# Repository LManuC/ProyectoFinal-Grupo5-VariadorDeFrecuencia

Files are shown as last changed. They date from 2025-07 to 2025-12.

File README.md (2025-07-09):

# ProyectoFinal-Grupo5-VariadorDeFrecuencia
El presente proyecto propone el desarrollo de un dispositivo electrónico capaz de alimentar un motor trifásico de hasta 1/3 HP, utilizando como fuente una tensión continua de 12V. Este conversor funciona como un variador de frecuencia, generando una salida trifásica con tensión eficaz entre fases de hasta 220 Vrms y frecuencia de salida variable entre 1 Hz y 150 Hz.
Para lograr el control del motor, se utiliza una técnica de modulación espacial (Space Vector Modulation), sin sensores montados en el eje del motor, lo que permite una instalación más sencilla, sin necesidad de encoder. El sistema está comandado por un controlador que gestiona tanto el disparo de los transistores como la interfaz de usuario y las protecciones internas.
El sistema estará contenido en una carcasa plástica especialmente diseñada para garantizar seguridad eléctrica durante la manipulación, proteger los componentes internos y permitir un montaje simple y robusto en el entorno de uso.

# Motivación
En un país como la Argentina, con grandes extensiones de tierras sin suministro eléctrico, la explotación de la energía renovable ha dado lugar a la utilización de grandes máquinas y herramientas eléctricas que tiempo atrás no hubiese sido posible. Si bien es cierto que los generadores eléctricos han dado espacio a estas instalaciones, requerían de mantenimiento periódico para que estuviesen operativas en el momento que se necesitaban, además de necesitar un material combustible que les permitiera funcionar y, en ocasiones podría generar un problema el ruido de los motores.

# Concepto del negocio
El dispositivo diseñado permitirá la conversión, acondicionamiento y regulación de la energía eléctrica para el accionamiento de un motor trifásico de baja potencia (1/3 HP) con velocidad variable generada a partir del motor de combustión interna y el alternador de equipos agrícolas o sistemas de energía solar, eólica con su correspondiente back up de energía eléctrica, posibilitando la operación de motores trifásicos destinados a tareas como sistemas de riego, transporte de materiales mediante cintas motorizadas o procesos de molienda integrados a bordo que puedan emplearse unificando todos los dispositivos que son empleados en instalaciones de energía renovable: Elevadores de tensión, inversores y variadores de frecuencia. La propuesta se enmarca en la necesidad de implementar soluciones energéticas autónomas y portátiles en entornos rurales, donde las condiciones de acceso a la red eléctrica convencional pueden ser limitadas o inexistentes.

## FODA

### Fortalezas
* La alimentación de baja tensión, nos permite meternos en un nuevo nicho. Permite trabajar con sistemas solares reducidos o baterías.
* Producto robusto y económico.
* Mantenimiento preventivo y reparación: Al conocer el diseño del equipo se puede hacer mantenimiento a los equipos y también otorgar una garantía con un taller de revisión y reparación en caso de falla.
* Productor local: Es una característica muy importante ya que el cliente tiene mayor confianza y los plazos de entrega son muchos más rápidos y económicos.
### Oportunidades
* Dada la practicidad puede ocasionar una gran demanda en zonas aisladas, remotas o rurales que se encuentren offgrid.
* Dado que es un único producto de su clase podría aparecer un nuevo rubro o sector diferente en donde encuentre utilidad. 
* El desarrollo nacional nos puede dar ventajas en licitaciones públicas o incentivos tecnológicos del gobierno.
### Debilidades
* Falta de experiencia y desconocimiento del producto puede desalentar o generar desconfianza en el producto.
* La robustez es muy importante en un controlador de un motor, se necesitan años de estudio riguroso del comportamiento y testeo del equipo para asegurar un funcionamiento ejemplar.
* La certificación eléctrica es un aspecto crucial en un equipo de esta clase y estas son muy costosas.
### Amenazas
* Posibilidad de la aparición de competencia con mejores precios y más funcionalidades.
* La escalabilidad no siempre es tan lineal, si aumenta mucho el mercado puede ocurrir que la inversión sea grande.
* El soporte post venta debe funcionar bien ya que en caso de una respuesta lenta al cliente podría perjudicar a la reputación de la marca.

# Alcance
El alcance del proyecto quedará definido en lograr, a partir de una fuente de de 12V de corriente contínua, el accionamiento de un motor trifásico de ⅓ de HP, variar su velocidad de giro, programar sesiones de trabajo diario, informar por señales típicas de 0-10V la velocidad de operación del motor, parada de emergencia, configuración de velocidades a través de un selector.

## Características eléctricas del dispositivo
Vin: 12VDC
Vout: 3 x 220VAC
fout: 0Hz - 150Hz
Pmax: 375W / 1/2HP

# Riesgos
1.  Fallas en la elección de la topología:
    -  Priorización del diseño frente a otras tareas;
    -  Ensayos varios sobre circuitos físicos;
2.  Rendimiento simulado insuficiente
    -  Priorización del diseño frente a otras tareas;
    -  Ensayos varios sobre circuitos físicos;
    -  Pruebas sobre motores utilizando variadores de frecuencia comerciales con entrada de contínua;
3.  No se consiguen los materiales en el mercado local
    -  Diseño temprano de PCB
    -  Compra en exceso de dispositivos críticos
4.  El transformador está mal construído y no entrega la potencia necesaria
    -  Fabricación de transformador con un proveedor especializado
5.  Al PCB le faltaron rutear una o más pistas
    -  Validaciones cruzadas de footprints
    -  Validaciones cruzadas de esquemáticos
    -  Validaciones cruzadas de PCB
6.  Pérdida de componentes
    -  Compra en exceso de dispositivos críticos
    -  Compra en exceso de dispositivos pequeños
    -  Compra en exceso de dispositivos sin marking
7.  Error en el diseño del footprint
    -  Validaciones cruzadas de footprints
    -  Checkbox en componentes para registrar validación
    -  Agregado de hoja de datos al esquemático
    -  Agregado de nombre del componente según el fabricante
8.  Errores de diseño hacen que la tensión no sea lo suficientemente alta
    -  Diseño autodefensivo con tensiones sobredimensionadas
    -  Cálculo de convertido con duty de respaldo
9. Rotura del banco de pruebas
    -  Fabricación de partes críticas de repuesto
    -  Colaboración externa especializada
10. Dificultades para simular el desfasaje
    -  Sobreestimación de los tiempos de trabajo
11. Error en el cálculo de la corriente máxima de algún componente y la corriente quedó sobredimensionada
    -  Justificación y documentación de los componentes elegidos
    -  Compra en exceso de dispositivos críticos
12. Falla el circuito y se quema una de las placas de potencia
    -  Fabricación de placa extra
    -  Compra en exceso de dispositivos críticos
    -  Circuitería de protección ruteada sin montar
13. El transformador está mal calculado y no entrega la potencia necesaria
    -  Ensayos exhaustivos durante el diseño
14. Ruido eléctrico interfiere en el display
    -  Fabricación de pantalla metálica para separar circuitos ruidosos
15. El motor no arranca por falta de potencia en la entrada
    -  Pruebas con batería de auto de respaldo

# Calidad

|Funcionalidad |  Importancia  |
|---|---|
|Tensión de salida |  16,3% |
|Tensión entrada |  20,7% |
|Frecuencia de salida | 7,1% |
|Protecciones contra sobrecorriente| 6,9% |
|Aislamiento entrada salida |  12,1% |
|Algoritmo modulación | 9,6% |
|Display con menú |  10,6% |
|GPIOs | 7,7% |
|Access point | 9,0% |

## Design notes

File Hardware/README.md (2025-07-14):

# Comunicación entre microcontraldores

## 1. UART (Universal Asynchronous Receiver/Transmitter)
_Tipo:_ Asíncrona

_Velocidad típica:_ Hasta 1 Mbps (aunque la mayoría trabaja entre 9600 y 115200 bps)

_Ventajas:_
* Muy simple de implementar (incluso por software si no hay hardware UART)
* No necesita reloj compartido

_Desventajas:_
* Sin verificación de integridad robusta
* Solo útil para distancias cortas

_Ideal para:_ Comunicación punto a punto a distancias cortas y baja/moderada velocidad

## 2. SPI (Serial Peripheral Interface)
_Tipo:_ Síncrona (requiere línea de reloj)

_Velocidad típica:_ De 1 a 20 Mbps (puede llegar a más dependiendo del microcontrolador)

_Ventajas:_
* Muy rápida
* Full duplex
* Buena para cortas distancias dentro de un mismo PCB

_Desventajas:_
* Requiere más pines (MOSI, MISO, SCLK y a veces CS)
* No hay detección de errores integrada

_Ideal para:_ Comunicación rápida entre micros en un mismo sistema o módulo

## Conclusión

Elegimos SPI por subre UART para poder aprovechar más la velocidad del bus. Creemos que la implemetación en software no debería cambiar entre una u otra, por lo que no habría una ventaja o desventaja de una sobre la otra.

Debemos tener el cuidado suficiente de la con la señal ya que, pese a ser un único producto y un ansamblado fijo, la comunicación se dará entre dos PCBs diferentes a través de un header.

# Pulsadores

Para el traclado matricial utilizaremos los pulsadores con vástago sobresaliente para poder enganchar con la tecla impresa.

# Teclado

Utilizar por lo menos 8 teclas, pero no más (o no mucho más de 10).

El Start y stop cuentan dentro de este teclaod matricial pero el botón golpe de puño para parada de emergencia iría aparte.

Usaríamos un relay para cortar en bus de contínua, comandado por la parada de emergencia y el STM32.

# Dimensiones

El gabinete va a tener un tamaño de 130mm x 325mm (Sujeto a modificaciones) para respetar una relación de aspecto de 2.5.

La idea sería incluir en la parte superior un cooler de 120mm de lado.

# Señales a medir por el ESP

* Nivel de tensión del bus de contínua
* Corriente del bus de contínua

# Conectores

## Señales para el ADC
1. 5V
2. GND
3. Corriente
4. Tensión
5. GND

## Comunicaciones
1. GND
2. NSS
3. SCK
4. MISO
5. MOSI

## Señales de una placa a la otra

1. 0-10V
2. Selección de velocidades
3. Start
4. Stop

## Botones de start y stop

Borneras externas para conectar pulsadores externos en caso de montar el gabinete del producto dentro de otro gabinete.

# Alimentación

1. +12V
2. GND

1. +5V
2. GND

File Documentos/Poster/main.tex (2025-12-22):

\def\footer#1{\def\insertfooter{#1}}
\documentclass[final]{beamer}

\usepackage[scale=1.150]{beamerposter}
\usetheme{MUWposter}

%Logo/Banner de la Empresa/Proyecto
\logo{
\pgfputat{
\pgfxy(-10,108)}{
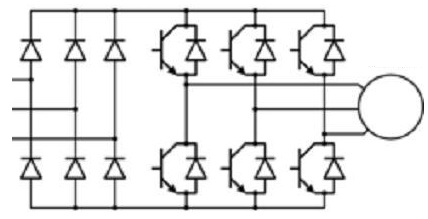
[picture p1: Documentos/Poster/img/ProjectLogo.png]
\pgfbox[center,base]{}
}
}  

\usepackage{multicol}
\usepackage{array}
\newcolumntype{L}{>{\arraybackslash}m{22cm}}
\newcolumntype{S}{>{\arraybackslash}m{5cm}}
\usepackage{pgf}  
\usepackage{mathtools}
\usepackage{amsmath, amsthm, amssymb, amsfonts}
\usepackage{exscale}
\usepackage{xcolor}
\usepackage{ushort}
\usepackage{setspace}
\usepackage[square,numbers]{natbib}
\usepackage{url}
\bibliographystyle{abbrvnat}
\renewcommand{\vec}[1]{\ushort{#1}}
\renewcommand{\vec}[1]{\mathbf{#1}}
\definecolor{greenMUW}{RGB}{60,191,174}
\definecolor{blueMUW}{RGB}{17,29,79}
\definecolor{skinMUW}{RGB}{254,228,217}
\definecolor{hellblauMUW}{RGB}{95,180,229}
\colorlet{themecolor}{greenMUW}
\usebackgroundtemplate{}

%-----------------------------------------------
%  Columnas
%-----------------------------------------------
\setlength{\paperwidth}{33.1in}
\setlength{\paperheight}{46.8in}
\newlength{\sepmargin}
\newlength{\sepwid}
\newlength{\onecolwid}
\newlength{\twocolwid}
\newlength{\threecolwid}
\setlength{\sepmargin}{0.055\paperwidth}
\setlength{\sepwid}{0.03\paperwidth}
\setlength{\onecolwid}{0.43\paperwidth}
\setlength{\twocolwid}{0.9\paperwidth}

%--------------------------------------------------------------------------------------
%	TITULO 
%--------------------------------------------------------------------------------------
\setbeamertemplate{title}[left]
\setbeamertemplate{frametitle}[default][left]

\title{CONTROLADOR DE MOTOR TRIFÁSICO PARA INSTALACIONES DE BAJA TENSIÓN} % Poster title
\author{Elian Andrenacci, Lucas Manuel Carra}
\institute{Universidad Tecnológica Nacional - Facultad Regional Buenos Aires \vspace{0.5cm} \linebreak
Cátedra Proyecto Final: Mg.Ing. Sebastián Verrastro, Mg.Ing. Pablo Sánchez, Mg.Ing. Mariano Vidal, Ing. Fernando Valenzuela}
%--------------------------------------------------------------------------------------

\begin{document}

  \addtobeamertemplate{block end}{}{\vspace*{1ex}}
  \addtobeamertemplate{block alerted end}{}{\vspace*{0ex}}
  \setlength{\belowcaptionskip}{2ex}
  \setlength\belowdisplayshortskip{1ex}
    
  \begin{frame}[t] 
      \begin{columns}[t] 	  
      \begin{column}{\sepmargin}\end{column}
      	  \begin{column}{\onecolwid}
		  \begin{block}{Objetivo}

          Fabricar un variador de frecuencia de un motor trifásico (3x220VAC) con potencia de salida máxima de 1/3HP con tensión de entrada de 12VDC desde 0 a 150Hz, para ser un controlador para zonas remotas o de difícil acceso sin la necesidad de la infraestructura de un proveedor de servicio eléctrico tradicional.
          Este dispositivo está diseñado para proveer a productores que tengan trabajos que se realicen dentro y fuera de plantas estables, que necesiten trasladar maquinarias de trabajo, pudiendo conservar instalaciones eficientes dentro y fuera de los espacios de trabajo tradicionales sin tener diversidad en la maquinaria empleada.
  
          \end{block}
          
          \begin{block}{Marco Teórico}
          Teniendo en cuenta la entrada de tensión disponible, es necesaria una etapa de conversión de tensión DC/DC que eleve la tensión al menos 26 veces y que pueda manejar potencias superiores a los 250 W. Si bien la topología puente completo tiene mejores características para el cumplimiento del objetivo, el convertidor push-pull resulta adecuado en convertidores de baja potencia (en el orden del 1kW) con un circuito de control más simplificado, aunque con un aprovechamiento menos eficiente del transformador.
          El variador de frecuencia tiene como función convertir el bus de corriente contínua en corriente alterna trifásica para el accionamiento del motor. Debido a la alta relación de tensión de la etapa de entrada del sistema, se implementa una modulación de vector espacial o \textit{SVM} que permite lograr la señal antes mencionada con una tensión de bus de contínua de 320 VDC. En comparación con el método PWM clásico, este tipo de modulación logra un mejor aprovechamiento del bus de contínua, reduce la distorsión armónica y optimiza la calidad de la forma de onda de salida, con efectos positivos sobre el funcionamiento del motor, tales como un régimen de operación más suave, menor calentamiento y una mayor eficiencia energética.
    
          \end{block}

          \begin{block}{Resultados}
          Durante las pruebas del sistema completo, se observó un excesivo calentamiento del transformador por encima de los 110°C, temperatura superior a la indicada por el fabricante del núcleo del transformador, pudiendo resultar en la rotura del mismo. El dispositivo tolera perfectamente una carga de 1/6HP por períodos prolongados de tiempo, manteniendo estables las tensiones y corrientes de cada fase alcanzando los 140 W, y durante 10 minutos 1/3HP debido a un error en el bobinado secundario del transformador.
          En un análisis posterior permitió identificar una incosistencia en el diseño del transformador, lo que explica el comportamiento térmico observado. Para corregir el problema se deberá rebobinar el transformador con un conductor extra en el bobinado del secundario, motivo por el cual, además, requerirá de un núcleo más grande que permita alojar la totalidad del bobinado.
          A pesar de esta limitación, se logró controlar el motor con trabajos programados, señales eléctricas externas, control y configuración desde una red Wi-Fi AP generada por el dispositivo y configurar y controlar su régimen de funcionamiento desde el panel frontal.

          \end{block}
          
          \begin{block}{Conclusiones}
          El proyecto cumple con los objetivos propuestos para un variador de fre-

         \end{block}
         \end{column}
         \begin{column}{\sepwid}  \end{column}
         \begin{column}{\onecolwid} %The second column
         
         \begin{block}{\vspace*{2.7cm}}
         cuencia trifásico alimentado desde baja tensión orientado a aplicaciones de potencia moderada. El sistema permite el control adecuado de un motor trifásico mediante modulación vectorial \textit{SVM}, logrando una generación de tensiones esperadas, un aprovechamiento del bus de contínua que permitió lograr la señal de salida sin una tensión del bus de contínua muy elevada y un comportamiento estable en régimen permanente.
          
        Demuestra una capacidad de sobrecarga limitada pero controlada: el variador es capaz de sostener una potencia del orden de 1/3 HP durante intervalos de tiempo reducidos, sin embargo, el sistema mantiene de forma confiable solo una potencia de 1/6 HP para operación continua, limitando la temperatura del transformador dentro de los límites seguros declarados por el fabricante del núcleo magnético.

        El sistema de control es bueno y confiable, lo que permite una buena base de trabajo para futuras mejoras y actualizaciones.
         \end{block}
          
          \begin{block}{ }
				\begin{figure}
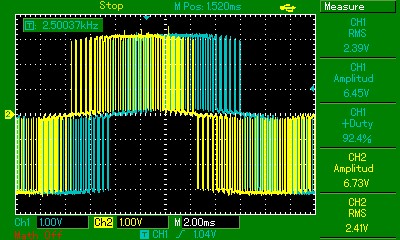
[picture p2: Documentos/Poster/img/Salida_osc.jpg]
                    
				\end{figure}
                
                \begin{multicols}{2}
                \begin{figure}
                	\vspace*{0.7cm}
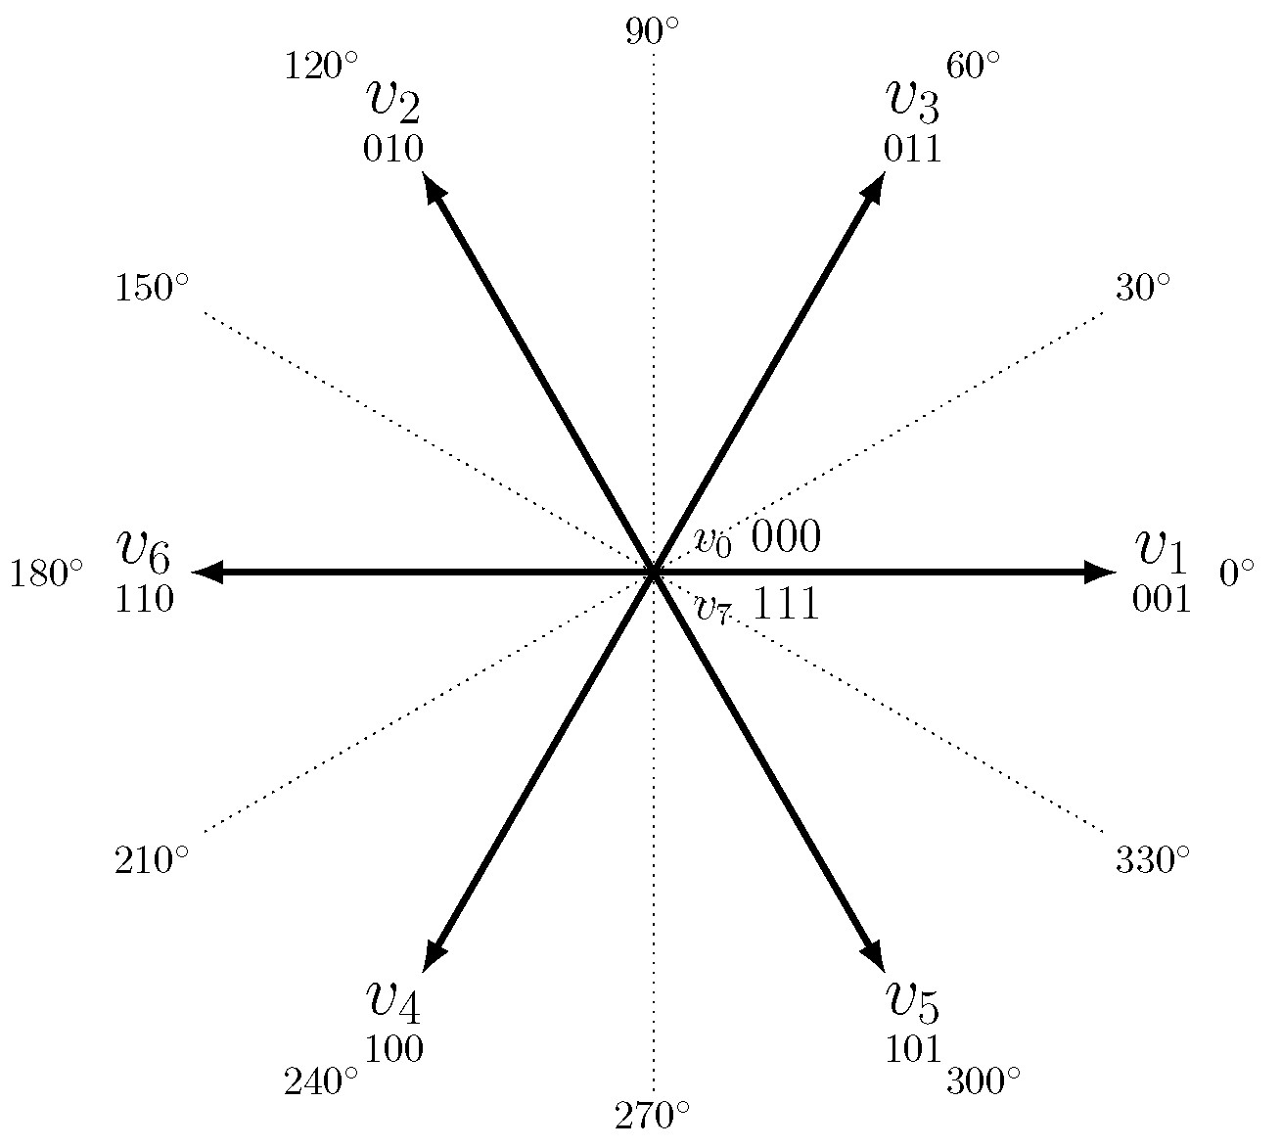
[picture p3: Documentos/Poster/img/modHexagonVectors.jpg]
                    
				\end{figure}
                \begin{figure}
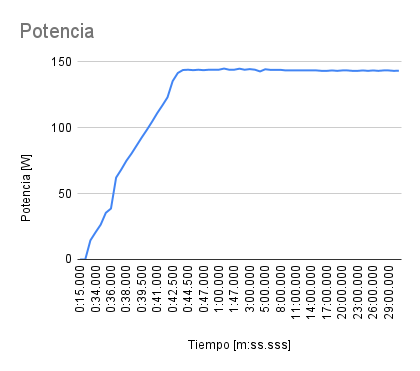
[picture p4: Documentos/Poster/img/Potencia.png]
                    
				\end{figure}
                \end{multicols}
                
                \begin{figure}
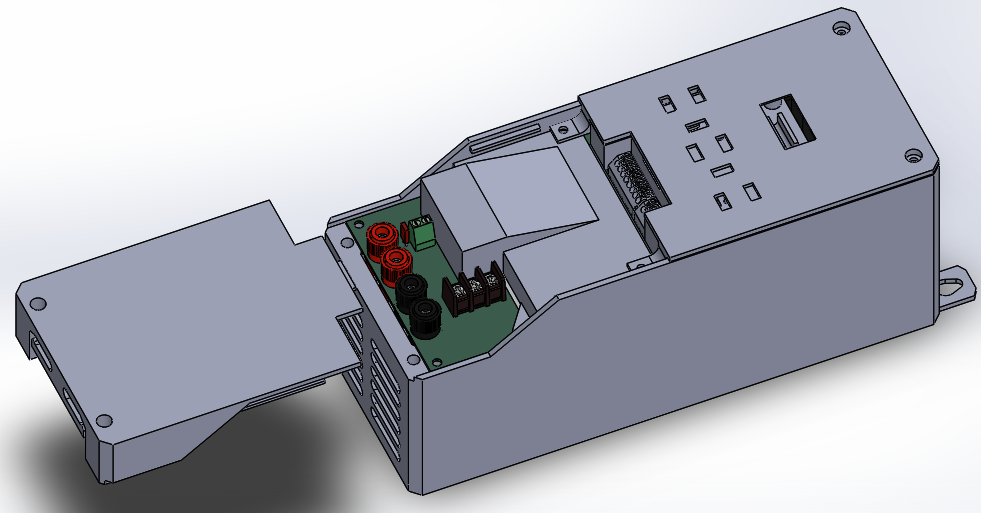
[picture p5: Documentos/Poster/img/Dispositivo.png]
                    
				\end{figure}
                
	  \end{block}
      \end{column}
      \begin{column}{\sepmargin} \end{column}
      \end{columns} 
      \begin{columns}[t]       
      \begin{column}{\sepmargin} \end{column}
      \begin{column}{\onecolwid}
			    \vspace*{-0.9cm}
				\begin{alertblock}{\large Contacto e Información}
                \vspace*{-0.5cm}
					\begin{footnotesize}
					\begin{itemize}
						\item {Proyecto Final - UTN-FRBA} - \href{Proyecto Final - UTN-FRBA}{https://www.frba.utn.edu.ar/electronica/proyecto-final/}
                        \item {Repositorio proyecto} - \href{Repositorio proyecto}{https://github.com/LManuC/ProyectoFinal-Grupo5-VariadorDeFrecuencia/}
                        \item {Canal de youtube con video de funcionamiento} - \href{Canal de youtube con video de funcionamiento}{https://www.youtube.com/playlist?list=PLN\_nehD\_w6V3k8sGirIR0Lm5y22pTkL74}
					\end{itemize}
				\end{footnotesize}			
				\end{alertblock}
		    \end{column}
			\begin{column}{\sepwid}\end{column} 
			\begin{column}{\onecolwid} 
              \begin{block}{\large Referencias}
			  \vspace*{-0.5cm}
              	\nocite{*}
					{\footnotesize
\begin{thebibliography}{9}

\bibitem{cita_1}
    Juan Carlos FLoriani
    \textit{"Fuentes conmutadas - Análisis y diseño"}
    Universidad Nacional del Litoral
    Argentina
    2010
    ISBN 987-9406-45-1

\bibitem{cita_2}
    Ayman Y. Yousef
    \textit{"Space Vector Pulse Width Modulation Technique"}
    Electrical Engineering Department, Faculty of Engineering at Shoubra
    Egypt
    2015
    ISSN 0976-1353

\end{thebibliography}
}
			\end{block} 
			\end{column}             
			\begin{column}{\sepmargin}\end{column}            
\end{columns}
\end{frame}	
\end{document}

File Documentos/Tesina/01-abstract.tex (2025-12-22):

\label{sec:1_abstract}

Este trabajo presenta el diseño, implementación y validación de un controlador de motor trifásico para instalaciones de baja tensión, compuesto por un convertidor DC-DC aislado y un inversor trifásico gobernado por modulación de vectores espaciales (SVM). El convertidor, de topología push-pull, eleva una entrada de 12 Vdc a un bus de continua de 320 Vdc, optimizando el uso del transformador de ferrita y los semiconductores. El inversor sintetiza tensiones trifásicas ajustables en frecuencia y amplitud para accionar un motor de inducción, manteniendo la relación V/f y priorizando la eficiencia con conmutación ordenada. El sistema incorpora una HMI basada en ESP32 con interfaz local (display SH1106, teclado matricial, expansión de GPIO con MCP23017) y configuración vía Wi-Fi; la lógica de control en STM32 se coordina mediante un enlace SPI maestro-esclavo. Se desarrollaron PCB dedicadas para potencia y control, con aislamiento galvánico y protecciones. Los ensayos funcionales abarcan integridad de la modulación, simetría de pulsos, índice de modulación y pruebas de rendimiento eléctrico y térmico, confirmando la viabilidad del enfoque para aplicaciones de bajo costo, mantenimiento simple y operación segura en ambientes de potencia moderada. El documento detalla criterios de diseño magnético, consideraciones constructivas, arquitectura de firmware y resultados de laboratorio.

Durante las pruebas experimentales se pudo comprobar una limitación térmica en la etapa de conversión, restringiendo la operación contínua a potencias del orden de 1/6HP, manteniendo la capacidad de sobrecarga transitoria de hasta 1/3HP.

\textbf{Palabras clave:} variador de frecuencia, SVM, push-pull, inversor trifásico, conversión DC-DC.

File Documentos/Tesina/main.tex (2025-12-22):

%%%%%%%%%%%%%%%%%%%%%%%%%%%%%%%%%%%%%%%%%%%%%%%%%%%%%%%%%%%%%%%%%%%%%%%%%%%%%%%%%%%%%%%
%%%     Build: pdflatex -aux-directory=out/build -output-directory=out main.tex     %%%
%%%%%%%%%%%%%%%%%%%%%%%%%%%%%%%%%%%%%%%%%%%%%%%%%%%%%%%%%%%%%%%%%%%%%%%%%%%%%%%%%%%%%%%

\documentclass[a4paper,10pt]{article}

% Paquetes
\usepackage{titlesec}
\usepackage{titling}
\usepackage{setspace}
\usepackage{graphicx}
\usepackage{caption}
\usepackage{subcaption}
\usepackage{float}
\usepackage{xcolor}
\usepackage[affil-it]{authblk}
\usepackage{soul}
\usepackage{array}
\usepackage{tabularx} % <<-- clave
% Idioma y codificación
\usepackage[spanish]{babel}
\usepackage[utf8]{inputenc}
\usepackage{csquotes}

% Configuraciones
%\setmainfont{Times New Roman}
\usepackage{newtxtext,newtxmath}
% Para que funcione correctamente con APA
\usepackage[style=apa, backend=biber]{biblatex}
\addbibresource{04-bibliografia.bib}
\DeclareLanguageMapping{spanish}{spanish-apa}

\usepackage[hidelinks]{hyperref}

\hypersetup{
    colorlinks,
    linkcolor={red!50!black},
    citecolor={blue!50!black},
    urlcolor={blue!80!black}
}

\begin{document}
\begin{titlepage}
\centering
\begin{figure}[t]
	\centering
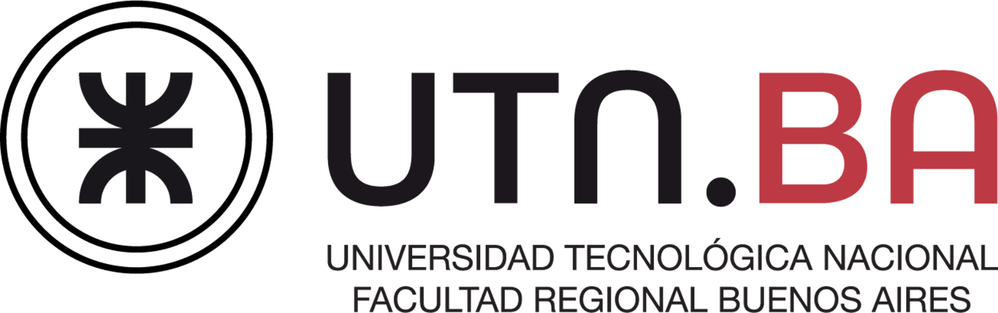
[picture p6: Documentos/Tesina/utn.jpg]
	
    \vspace{0.5cm}
\end{figure}%
	{\LARGE Proyecto Final\par}
    {\LARGE 2025\par}
	\vspace{1cm}
	{\huge\bfseries Controlador de motor trifásico para instalaciones de baja tensión\par}
	\vspace{1cm}
    {\LARGE Tesina\par}
    \vspace{1cm}
	{\Large\itshape Elian Andrenacci, Lucas Manuel Carra\par}
	\vfill
\end{titlepage}

\tableofcontents

\newpage
\section{Abstract}
\input{01-abstract.tex}

\section{Marco teórico}
\input{mt/cnv/cnv.tex}
\input{mt/motor/motor.tex}
\input{mt/inv/inv.tex}
\input{mt/hmi/hmi.tex}
\input{mt/mod/mod}

\section{Desarrollo de proyecto}
\input{dev/cnv/cnv.tex}
\input{dev/inv/inv.tex}
\input{dev/hmi/hmi.tex}
\input{dev/mod/mod.tex}
\input{dev/mont/mont}

\section{Ensayos y Verificación}
\input{ens/ens.tex}

\section{Conclusiones}
\input{02-conclusion.tex}

\newpage
\section{Bibliografía}
\label{sec:7_bib}
\nocite{SVM_Strobl}
\nocite{DesignAndOptimization_Wang}
\nocite{IsolationInACMotorDrivers}
\nocite{AnIsolatedMosfetGateDriver_Walker}
\nocite{IsolatedMultipleOutputFlybacj}
\nocite{DigitalMotorContol_TI}
\nocite{SoftSwitchingSnubber_Zhang}
\nocite{THDAndTorqueRipple_Sieklucki}
\nocite{H-BridgeMultilevelInverter_Nagle}
\nocite{StructureMultilevelConverter_Zare}
\printbibliography[heading=none]

\newpage
\section{Índice de Figuras y Tablas}
\label{sec:7b_indice}

\listoffigures
\listoftables

\newpage
\section{Anexo}
\input{anexo/cnv/cnv.tex}
\input{anexo/costos/costos}

\end{document}

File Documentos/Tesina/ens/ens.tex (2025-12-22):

\label{sec:4_ens}

\subsection{Introducción}

En esta sección se presentan los ensayos experimentales realizados sobre el variador de frecuencia desarrollado. El objetivo de estas pruebas es verificar el correcto funcionamiento del dispositivo en condiciones reales de operación, evaluar su respuesta ante distintas cargas y frecuencias, y garantizar que los parámetros eléctricos se mantengan dentro de límites seguros.

Los ensayos permitieron comprobar tanto el desempeño del conversor, como el comportamiento del inversor, en esto se involucra la conmutación de los MOSFET, la modulación (SVM) implementada y el programa de control.

\subsection{Ensayo funcional}

El primer ensayo consistió en verificar el funcionamiento general del variador de frecuencia (VFD). Para ello, se conectó el motor trifásico al inversor y se alimentó la etapa de potencia mediante dos fuentes de $12V$ repartiendo la carga. Adicionalmente, se utilizó una tercera fuente destinada exclusivamente a la electrónica de control. La configuración del ensayo se muestra en el siguiente diagrama y en la imagen del banco de pruebas.

\begin{figure}[H]
\centering
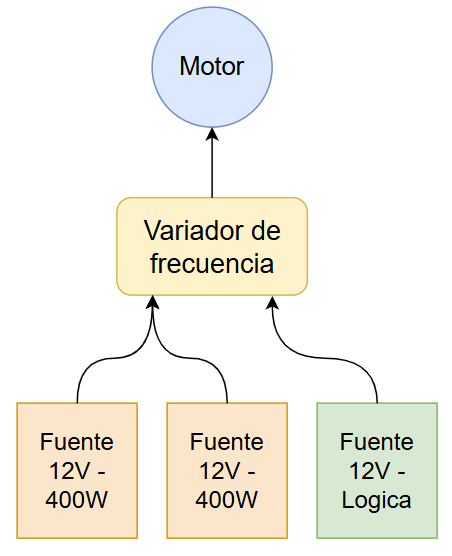
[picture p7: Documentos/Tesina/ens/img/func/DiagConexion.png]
    
    \caption{Diagrama de conexión para los ensayos.}
\label{fig:img_ens_func_diagConex}
\end{figure}

\begin{figure}[H]
\centering
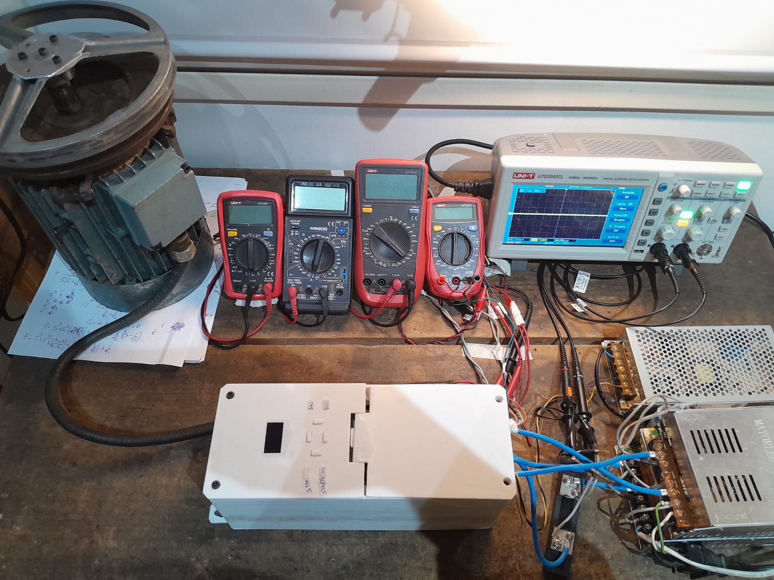
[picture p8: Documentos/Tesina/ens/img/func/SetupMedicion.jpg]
    
    \caption{Configuración de mediciones con el motor a la izquierda y las fuentes de alimentación a la derecha.}
\label{fig:img_ens_func_setup}
\end{figure}

Una vez energizado el sistema, se evaluó el comportamiento del motor durante las etapas de arranque, detención y régimen permanente, para frecuencias de operación comprendidas entre 10 Hz y 150 Hz. Durante todas las pruebas no se observaron vibraciones ni comportamientos anómalos en el motor, lo que indica que el sistema trifásico generado se encontraba correctamente balanceado y sin fallas de modulación.

También se aplicó carga al motor utilizando el freno dinámico, generando una potencia de salida aproximada de $300 W$. El motor respondió correctamente bajo estas condiciones, sin presentar inestabilidades ni síntomas de sobrecarga. Sin embargo, el sistema de frenado no permite realizar ensayos prolongados debido a limitaciones propias del mecanismo.

Es importante aclarar que el motor utilizado en la prueba es de $2 HP$, una potencia significativamente superior. No obstante, siempre que la carga aplicada no supere la potencia nominal, el comportamiento dinámico y eléctrico es representativo, por lo que los resultados obtenidos se consideran válidos para el análisis.

\begin{figure}[H]
\centering
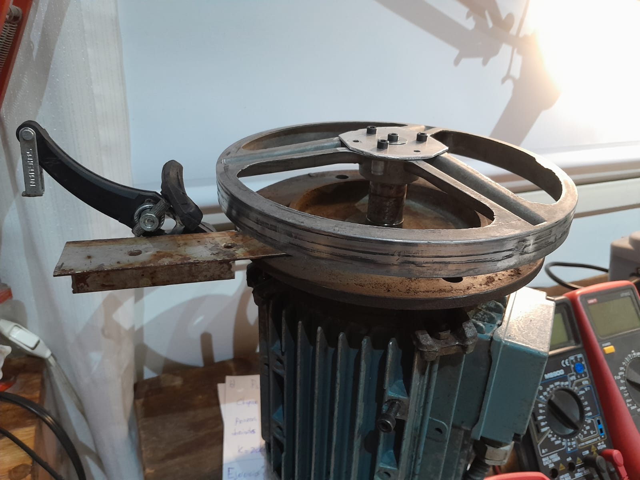
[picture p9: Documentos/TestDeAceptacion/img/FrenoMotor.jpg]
    
    \caption{Motor con un sistema de frenado ajustable.}
\label{fig:img_ens_func_frenoMotor}
\end{figure}

Asimismo, se comprobó el correcto funcionamiento de todas las entradas digitales, incluyendo los botones de comando y el circuito de parada de emergencia, verificando una respuesta inmediata y conforme a lo previsto en el diseño.

\begin{figure}[H]
\centering
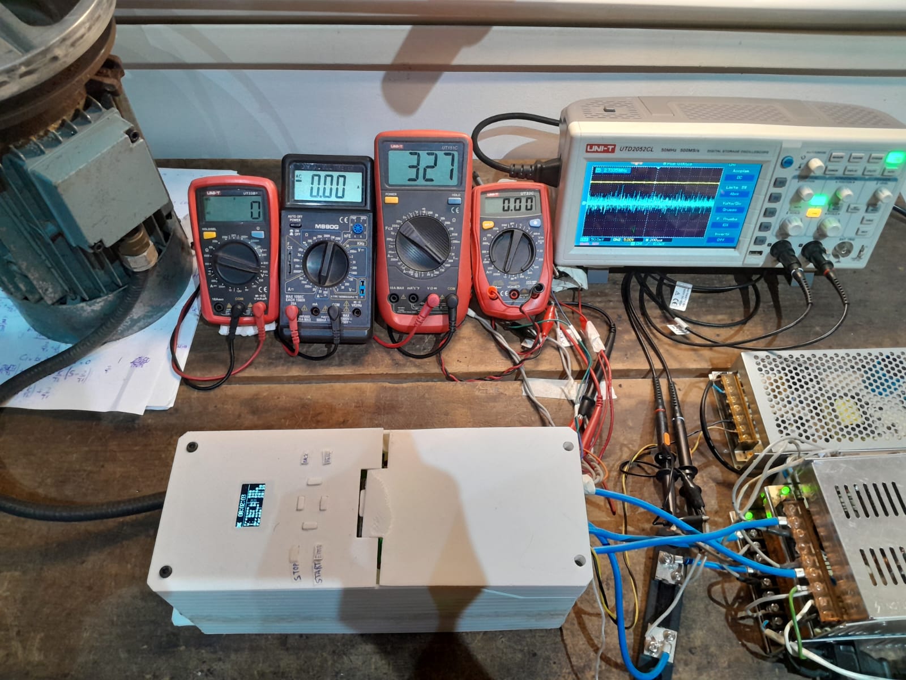
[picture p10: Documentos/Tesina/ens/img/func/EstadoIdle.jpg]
    
    \caption{Variador encendido en estado de espera.}
\label{fig:img_ens_func_estadoIdle}
\end{figure}

\subsection{Ensayo de la modulación}

Este ensayo tuvo como finalidad verificar el correcto funcionamiento del esquema de modulación por vector espacial (SVM). En primera instancia se evaluó la integridad de las señales generadas por el inversor, comprobando que las formas de onda presentaran la secuencia, el desfase y la calidad esperada sin distorsiones relevantes. Posteriormente, se analizaron parámetros asociados a la modulación, como la simetría de los pulsos y los tiempos de conmutación, cuya correcta implementación resulta esencial para evitar la aparición de armónicos y asegurar un funcionamiento estable del motor. Finalmente, se verificó que el índice de modulación respetara la estrategia $V/f$, garantizando la adecuada relación entre la frecuencia programada y la amplitud de tensión entregada al motor.

\subsubsection{Integridad de la señal}

En esta sección se evalúa el comportamiento de las formas de onda generadas por el inversor. Utilizando la masa del osciloscopio sobre una de las fases y muestreando las otras dos, se verificó la integridad de la señal entregada. A continuación se muestran mediciones realizadas con una frecuencia de salida de $50Hz$, donde puede observarse el desfase de $60^\circ$ entre fases característico del sistema trifásico.

\begin{figure}[H]
\centering
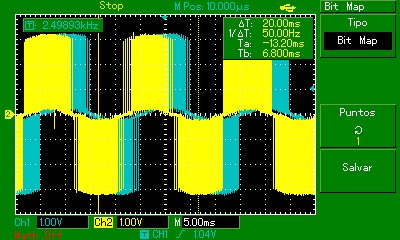
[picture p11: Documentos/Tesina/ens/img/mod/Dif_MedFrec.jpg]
    
    \caption{Forma de onda trifásica muestreando solo dos ondas de $50Hz$.}
\label{fig:img_ens_mod_Dif_MedFrec}
\end{figure}

\begin{figure}[H]
\centering
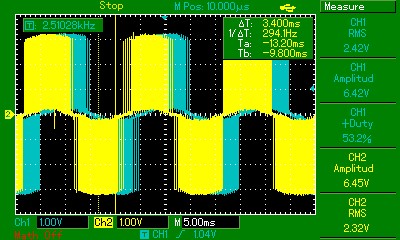
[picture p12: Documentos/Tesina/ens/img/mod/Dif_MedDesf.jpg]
    
    \caption{Desfase de $60^\circ$ entre dos fases medidas.}
\label{fig:img_ens_mod_Dif_MedDesf}
\end{figure}

También se registraron señales a distintas frecuencias para observar el comportamiento general de la modulación.

\begin{figure}[H]
\centering
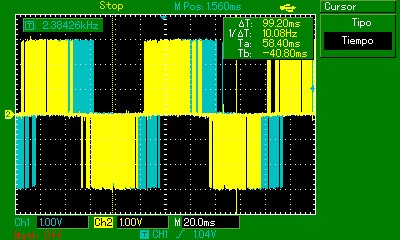
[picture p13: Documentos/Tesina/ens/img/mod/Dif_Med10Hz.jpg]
    
    \caption{Forma de onda a una frecuencia de $10Hz$.}
\label{fig:img_ens_mod_Dif_Med10Hz}
\end{figure}

\begin{figure}[H]
\centering
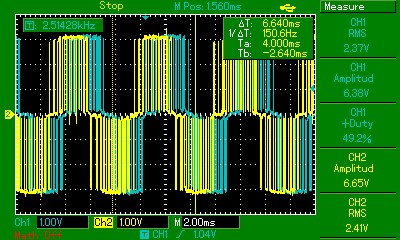
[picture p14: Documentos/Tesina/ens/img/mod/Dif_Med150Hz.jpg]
    
    \caption{Forma de onda a una frecuencia de $150Hz$.}
\label{fig:img_ens_mod_Dif_Med150Hz}
\end{figure}

Para un análisis más detallado, se realizó un acercamiento (zoom) sobre los pulsos de modulación.

\begin{figure}[H]
\centering
    
    \caption{Detalle ampliado de la modulación SVM (vista 1).}
\label{fig:img_ens_mod_Dif_Zoom1}
\end{figure}

\begin{figure}[H]
\centering
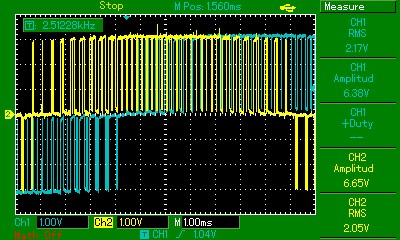
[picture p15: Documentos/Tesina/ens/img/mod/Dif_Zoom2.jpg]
    
    \caption{Detalle ampliado de la modulación SVM (vista 2).}
\label{fig:img_ens_mod_Dif_Zoom2}
\end{figure}

\subsubsection{Simetría de pulsos}

En esta sección se analiza la simetría de los pulsos generados por el esquema SVM, ya que cualquier asimetría podría introducir armónicos no deseados y producir vibraciones o ruidos en el motor. Las siguientes imágenes muestran capturas temporales de los pulsos, evidenciando su correcta simetría.

\begin{figure}[H]
\centering
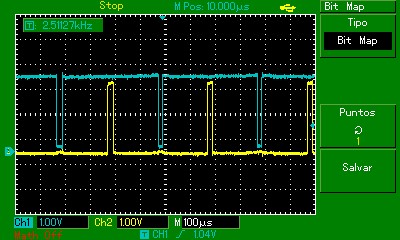
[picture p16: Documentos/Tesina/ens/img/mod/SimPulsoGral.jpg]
    
    \caption{Vista general de los pulsos de modulación generados por el microcontrolador.}
\label{fig:img_ens_mod_SimPulso_Gral}
\end{figure}

En las siguientes figuras se muestran dos mediciones, centradas respecto del pulso de otra fase, donde se observa que no existe diferencia apreciable en los tiempos de conmutación.

\begin{figure}[H]
\centering
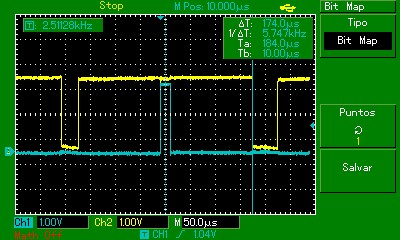
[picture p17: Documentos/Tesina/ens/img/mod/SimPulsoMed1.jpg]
    
    \caption{Comparación temporal de pulsos entre dos fases (vista 1).}
\label{fig:img_ens_mod_SimPulso_Med1}
\end{figure}

\begin{figure}[H]
\centering
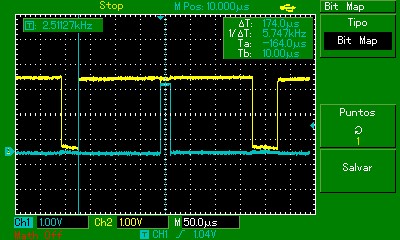
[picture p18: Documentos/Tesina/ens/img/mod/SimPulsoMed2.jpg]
    
    \caption{Comparación temporal de pulsos entre dos fases (vista 2).}
\label{fig:img_ens_mod_SimPulso_Med2}
\end{figure}

\subsubsection{Indice de modulación}

Para verificar la correcta implementación de la estrategia $V/f$, se evaluó la relación entre la frecuencia programada y la tensión eficaz aplicada al motor. Dado que el motor requiere una tensión proporcional a la frecuencia de operación, este ajuste se logra desde la modulación, reduciendo el ancho de los pulsos conforme disminuye la frecuencia.

Para este ensayo se montó el motor y se configuró el variador a distintas frecuencias fijas. En cada caso se midió la tensión de salida del inversor, registrando el comportamiento del sistema ante variaciones de frecuencia. Las figuras siguientes muestran el montaje experimental y las mediciones obtenidas.

En el ensayo se emplearon cuatro multímetros, destinados a medir:

\begin{enumerate}
    \item Tensión de linea del inversor.
    \item Corriente de fase.
    \item Tensión del bus DC.
    \item Corriente del bus DC.
\end{enumerate}

A continuación, se muestran imágenes del ensayo en donde se verifica esta relación.  

\begin{figure}[H]
\centering
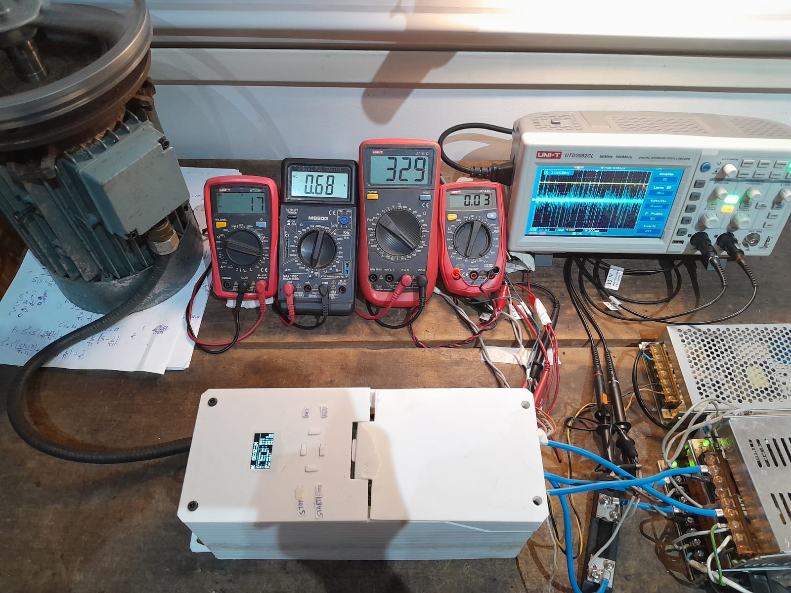
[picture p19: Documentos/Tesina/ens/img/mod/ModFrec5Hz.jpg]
    
    \caption{Variador con motor en vacío inyectando una señal de $5Hz$.}
\label{fig:img_ens_modInx_5Hz}
\end{figure}

\begin{figure}[H]
\centering
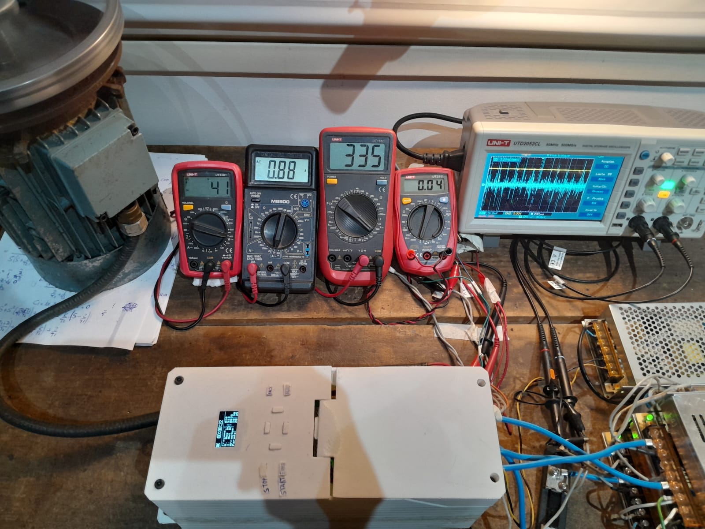
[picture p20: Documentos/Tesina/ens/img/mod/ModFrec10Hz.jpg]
    
    \caption{Variador con motor en vacío inyectando una señal de $10Hz$.}
\label{fig:img_ens_modInx_10Hz}
\end{figure}

\begin{figure}[H]
\centering
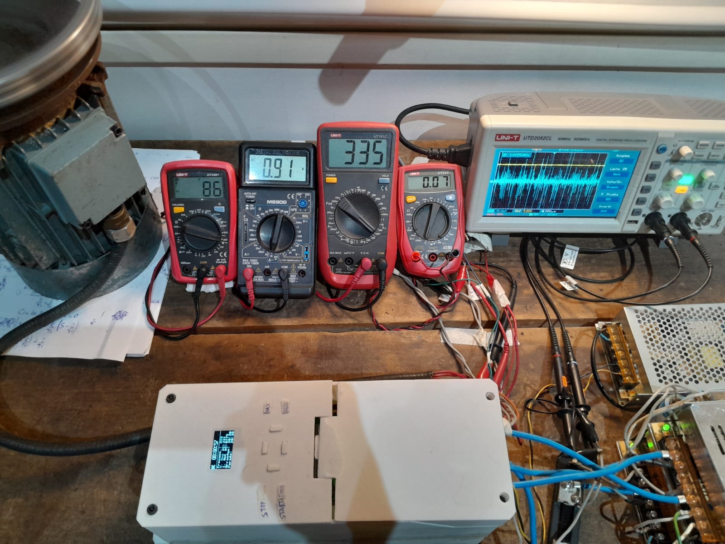
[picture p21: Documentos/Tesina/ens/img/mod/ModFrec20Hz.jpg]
    
    \caption{Variador con motor en vacío inyectando una señal de $20Hz$.}
\label{fig:img_ens_modInx_20Hz}
\end{figure}

\begin{figure}[H]
\centering
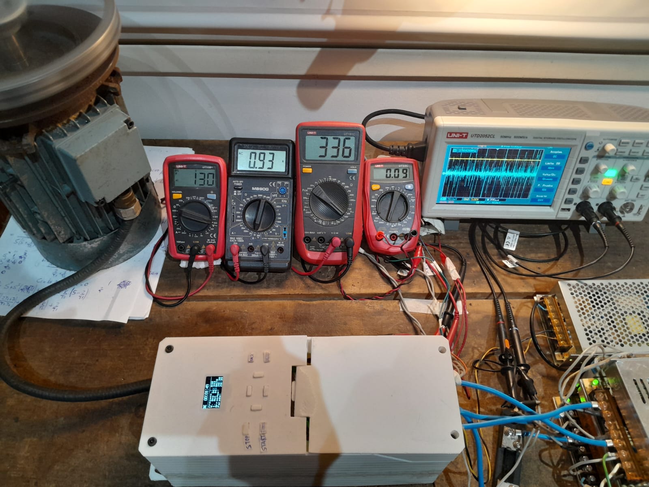
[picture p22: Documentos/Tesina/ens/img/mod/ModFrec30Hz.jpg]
    
    \caption{Variador con motor en vacío inyectando una señal de $30Hz$.}
\label{fig:img_ens_modInx_30Hz}
\end{figure}

\begin{figure}[H]
\centering
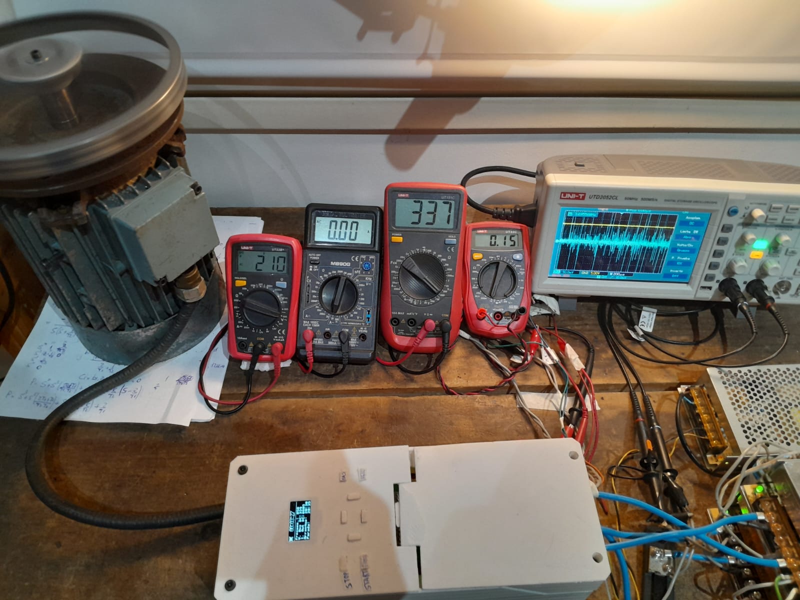
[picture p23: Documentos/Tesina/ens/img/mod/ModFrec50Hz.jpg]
    
    \caption{Variador con motor en vacío inyectando una señal de $50Hz$.}
\label{fig:img_ens_modInx_50Hz}
\end{figure}

\subsection{Rendimiento}

El análisis del rendimiento del sistema se realizó mediante un ensayo dividido en dos etapas. En la primera se evaluó el conversor, donde se midieron las tensiones y corrientes de entrada, así como el comportamiento del bus DC bajo carga inductiva. En la segunda etapa se analizó el inversor, utilizando una carga resistiva de valor conocido, lo que permitió evaluar únicamente la tensión de línea sin depender de mediciones de corriente.

La separación del ensayo en dos partes se realizo porque las mediciones de corriente en la salida del inversor no arrojaban resultados físicamente coherentes. Esto se relaciona con la naturaleza pulsante de la conmutación PWM, generando valores erróneos. Por tal motivo, las mediciones de corriente fueron descartadas.

Para la medición de la eficiencia se utilizó el motor junto con el freno dinámico, permitiendo evaluar el comportamiento del sistema en dos puntos de carga distintos. De este modo fue posible analizar la respuesta del conversor bajo diferentes demandas de potencia. Durante los ensayos, la frecuencia de salida del inversor se fijó en 50 Hz, asegurando una condición de funcionamiento estable y comparable entre las mediciones realizadas.

\subsubsection{Eficiencia del conversor}
En una primera instancia se ensayó el conversor bajo una condición de baja potencia de salida. Para medir la corriente de entrada se realizó una medición indirecta utilizando una resistencia de $0.1\Omega$ y observando la caída de tensión sobre la misma mediante el osciloscopio.

\begin{figure}[H]
\centering
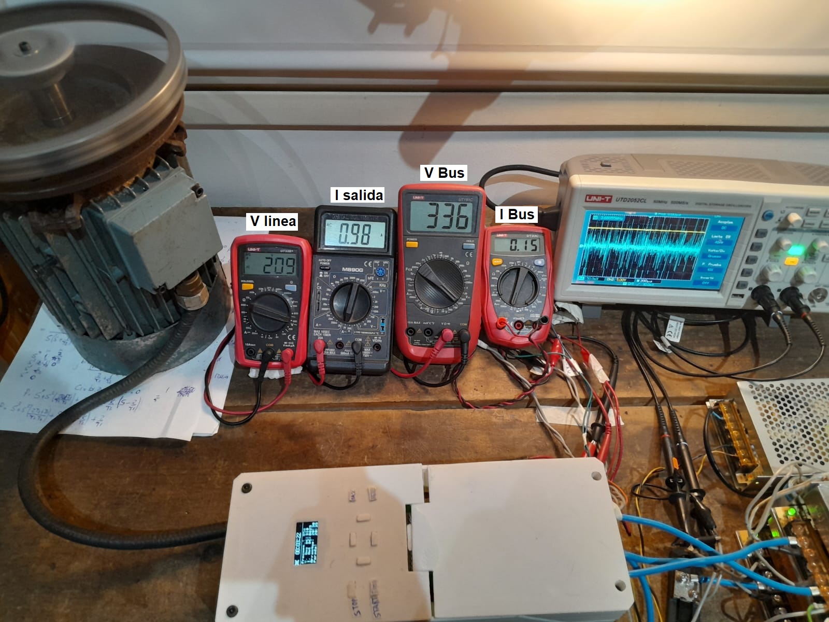
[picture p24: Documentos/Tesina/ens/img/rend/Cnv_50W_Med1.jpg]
    
    \caption{Medición con motor en vacío inyectando una señal de $50Hz$.}
\label{fig:img_ens_rend_cnv50W_med1}
\end{figure}

A partir de las mediciones de corriente y tensión de entrada se observa que la tensión de línea se mantiene prácticamente constante, mientras que la corriente presenta una forma de onda de diente de sierra. La frecuencia principal de esta señal es de $2.5 kHz$, coincidiendo con la frecuencia de conmutación asociada a la reposición de energía en el bus DC: cuando la tensión del capacitor disminuye por la demanda del inversor, el conversor incrementa la corriente para restaurar el nivel de tensión.

\begin{figure}[H]
\centering
    
    \caption{Medición de la tensión en shunt en trazo celeste y tensión de la fuente de alimentación en amarillo.}
\label{fig:img_ens_rend_cnv50W_med2}
\end{figure}

Las mediciones presentan un nivel elevado de ruido eléctrico, consecuencia tanto de la conmutación del inversor como de la del propio conversor, cuya frecuencia de switching es de aproximadamente $50 kHz$. Este ruido dificulta la obtención de mediciones más estables, aunque los valores promedio resultan representativos.

A partir del análisis de la señal se obtiene una corriente RMS de entrada de $2.9A$, lo que permite estimar una potencia de entrada de aproximadamente $66 W$. En cuanto al bus DC, se midió una tensión de $336 V$ y una corriente cercana a $150 mA$, resultando en una potencia de salida de $50.4W$. De este modo, el rendimiento del conversor para esta carga se calcula como

\[
\eta_{conversor \ - \ 50W} = \frac{P_{out}}{P_{in}}=0.764
\]

Posteriormente se repitió el mismo procedimiento para una carga cercana a 300 W, lo que permitió evaluar el desempeño del conversor bajo una condición de demanda más elevada. Debido a que la corriente del primario es significativamente mayor, se empleó una resistencia shunt de $1.5m\Omega$.

\begin{figure}[H]
\centering
    
    \caption{Medición con motor bajo carga inyectando una señal de $50Hz$.}
\label{fig:img_ens_rend_cnv300W_med1}
\end{figure}

\begin{figure}[H]
\centering
    
    \caption{Medición de la tensión en shunt en trazo celeste y tensión de la fuente de alimentación en amarillo.}
\label{fig:img_ens_rend_cnv300W_med2}
\end{figure}

En este caso se observa que la señal de corriente mantiene la forma de diente de sierra, pero con una frecuencia considerablemente más alta, cercana a los $50kHz$, correspondiente a la frecuencia de conmutación del conversor. A partir de estas mediciones se calcula una corriente de entrada de $69.33A$, lo que implica una potencia de entrada de $358.8W$.

Por su parte, en el bus de continua se mide una tensión de $333V$ y una corriente de $920mA$, obteniéndose así una potencia de $306.53W$.

\[
\eta_{conversor \ - \ 300W} = \frac{P_{out}}{P_{in}}=0.854
\]

Bajo una carga elevada, el conversor muestra un comportamiento más eficiente, lo cual resulta especialmente relevante dado que es en estas condiciones cuando se produce el mayor consumo de potencia.

\subsubsection{Eficiencia del inversor}

Dado que no se dispone de una forma confiable de medir la corriente y la tensión a la salida del inversor debido al elevado nivel de ruido y a las mediciones erróneas que este produce. No es posible calcular directamente la potencia de salida, y por lo tanto tampoco el rendimiento. Para resolver esta limitación, se utilizó una carga resistiva pura de valor conocido. Esta carga consume aproximadamente $120W$ en un sistema trifásico. Con el fin de determinar la potencia exacta, se midió la tensión de línea junto con la potencia entregada por el Bus DC.

\begin{figure}[H]
\centering
    
    \caption{Medición del variador con una carga resistiva pura de $120W$.}
\label{fig:img_ens_rend_inv120W}
\end{figure}

La potencia suministrada por el Bus DC es de $137.17W$, calculada a partir de una tensión de $334V$ y una corriente de $460mA$. La potencia de salida medida es de $130.63W$, lo que resulta en un rendimiento del $95.2\%$.

\[
\eta_{inversor \ - \ 120W} = \frac{P_{out}}{P_{in}}=0.9523
\]

\subsubsection{Rendimiento del variador}

El rendimiento total del variador está determinado por la combinación del rendimiento del conversor y del inversor. A partir de los valores, se obtiene un rendimiento de $81.3\%$. Si bien este valor es relativamente bajo, se encuentra fuertemente condicionado por el desempeño limitado del conversor, que constituye la principal fuente de pérdidas dentro del sistema.

\subsection{Durabilidad}

Para garantizar el funcionamiento continuo del sistema, se realizó un ensayo de durabilidad en el cual el variador fue exigido con una carga de $120W$ durante un período de $30$ minutos. Los resultados obtenidos demostraron que el equipo es capaz de soportar sin inconvenientes una carga equivalente a $1/6\text{HP}$ durante intervalos prolongados de operación.

No obstante, durante este ensayo se identificaron limitaciones en la etapa conversora, evidenciadas por un incremento significativo de la temperatura del transformador, la cual alcanzó los $112^\circ\text{C}$. Este valor representa el límite máximo admisible para garantizar un funcionamiento seguro, debido a la degradación en la aislación del bobinado. Cabe destacar que esta problemática no se encuentra asociada a una deficiencia en el sistema de refrigeración, sino que responde principalmente a un diseño no óptimo del transformador utilizado en la etapa conversora.

\begin{figure}[H]
\centering

\caption{Ensayo de durabilidad del dispositivo luego de $26$ minutos de operación con una carga de $120W$.}
\label{fig:img_ens_durabilidad}
\end{figure}

Los instrumentos visualizados en la pantalla permiten monitorear las siguientes magnitudes:

\begin{itemize}
\item Temperatura del disipador principal.
\item Tensión sobre la resistencia shunt del bus DC.
\item Tensión del bus DC.
\item Tensión alterna eficaz de salida.
\item Temperatura del transformador.
\end{itemize}

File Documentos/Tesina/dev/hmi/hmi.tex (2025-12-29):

\subsection{HMI} \label{sec:3_dev_hmi}

\subsubsection{Fuente de alimentación}

    El circuito aislado consta del regulador B1205S-2WR2, con una tensión de entrada de 10.8 a 13.2Vdc y una salida de 5Vdc, lo que permite completar el esquema con un regulador lineal de 3.3Vdc tradicional sin inconvenientes. Se optó por una circuitería como la de la figura~\ref{fig:imgDCDC_PS}.

    \begin{figure}[H]
        \centering
            
            \caption{Diagrama de la fuente de alimentación de la etapa de control.}
        \label{fig:imgDCDC_PS}
    \end{figure}

    Sumando los consumos de corriente pesimistas y aproximados de los componentes más importantes se obtiene:

    \begin{table}[H]
        \centering
        \begin{tabular}{ | c | c | c | c | c |}
        \hline
        Componente & Función                                    & Consumo [mA]  & Cantidad  & Total [mA]    \\ \hline
        STM32      & Microcontrolador variador                  & 150           & 1         & 150           \\ \hline
        ESP32      & Microcontrolador HMI                       & 500           & 1         & 500           \\ \hline
        MCP23017   & Expansor de GPIO                           & 1             & 1         & 1             \\ \hline
        SH1106     & Controlador de display y display OLED      & 120           & 1         & 120           \\ \hline
        Buzzer     & Indicador de pulsada panel frontal         & 30            & 1         & 30            \\ \hline
        Leds       & Indicadores testigo                        & 5             & 5         & 25            \\ \hline
        \multicolumn{4}{|r|}{Total}                                                         & 826           \\ \hline
        \end{tabular}
        \caption{Tabla de consumos}
    \end{table}

    Incluso, sin agregar un margen de seguridad del 20\%, se obtendría un consumo total de 991mA, superando los 800mA que un regulador lineal SMD como el AMS1117 podría llegar a tolerar sin ponerlo en riesgo. Dada esta condición, se decidió colocar dos fuentes gemelas. Una de ellas alimentará el microcontrolador que administra la señal de los transistores de salida junto con sus led testigos, la otra abastecerá al microcontrolador del HMI, sus periféricos y leds testigos:

    \begin{table}[H]
        \centering
        \begin{tabular}{ | c | c | c | c | c  |}
        \hline
        Componente  & Función                                   & Consumo [mA]  & Cantidad  & Total [mA]    \\  \hline
        STM32       & Microcontrolador variador                 & 150           & 1         & 150           \\ \hline
        Leds        & Indicadores testigo                       & 3             & 5         & 15            \\ \hline
        \multicolumn{4}{|r|}{Total}                                                         & 165           \\ \hline
        \end{tabular}
        \caption{Tabla de consumos}
    \end{table}

    \begin{table}[H]
        \centering
        \begin{tabular}{ | c | c | c | c | c  |}
        \hline
        Componente  & Función                                   & Consumo [mA]  & Cantidad  & Total [mA]    \\  \hline
        ESP32       & Microcontrolador HMI                      & 500           & 1         & 500           \\ \hline
        MCP23017    & Expansor de GPIO                          & 1             & 1         & 1             \\ \hline
        SH1106      & Controlador de display y display OLED     & 120           & 1         & 120           \\ \hline
        Buzzer      & Indicador de pulsada panel frontal        & 30            & 1         & 30            \\ \hline
        Leds        & Indicadores testigo                       & 2             & 5         & 10            \\ \hline
        \multicolumn{4}{|r|}{Total}                                                         & 661           \\ \hline
        \end{tabular}
        \caption{Tabla de consumos}
    \end{table}

    De esta manera se logra, adicionando ese mismo margen del 20\% 198mA y 793mA respectivamente, cumpliendo con la limitación antes mencionada. Así se llega a un diseño de PCB como el de la siguiente figura~\ref{fig:imgDCDC_PS_PCB}.

    \begin{figure}[H]
        \centering
            
            \caption{Diseño PCB de la fuente de alimentación.}
        \label{fig:imgDCDC_PS_PCB}
    \end{figure}

    \begin{figure}[H]
        \centering
            
            \caption{Diseño 3D de la fuente de alimentación.}
        \label{fig:imgDCDC_PS_PCB_3D}
    \end{figure}

\subsubsection{Estructura del código}

    Para el desarrollo del código del HMI se basó en freeRTOS sobre el framework del ESP32 de Espressif. Se hizo un desmembramiento de las distintas funcionalidades hasta llegar a una estructura atómica de tareas, cada una con un periférico y función específica que se comunica a través de diferentes queues y semáforos. La figura~\ref{fig:imgEstructuraDelCodigo} muestra las conexiones entre cada tarea y bloque funcional.

    \begin{figure}[H]
        \centering
            
            \caption{Esquema de comunicación entre módulos de código.}
        \label{fig:imgEstructuraDelCodigo}
    \end{figure}

\subsubsection{Display}

    El diseño de PCB del display no reviste demasiado desarrollo, basta con mencionar que se conectan solamente los pines SDA, SCL y alimentación tal como muestra la figura~\ref{fig:imgSH1106ConnectionKiCAD} y figura~\ref{fig:imgSH1106ConnKiCADPCB} debido a la utilización del módulo comercial del SH1106.

    \begin{figure}[H]
        \centering
            
            \caption{Conexionado de display en PCB.}
        \label{fig:imgSH1106ConnectionKiCAD}
    \end{figure}
    
    \begin{figure}[H]
        \centering
            
            \caption{Conexionado de display en PCB.}
        \label{fig:imgSH1106ConnKiCADPCB}
    \end{figure}

    \paragraph{Desarrollo del software} Para el control del display se trabajó con una tarea específica llamada \textit{task\_display},donde se lo inicializa junto al puerto $I^{2}C$; se reciben señales desde el panel frontal o el control del sistema del variador de frecuencia a través de colas de comandos para ingresar al menú, navegarlo, editar variables ,guardarlas en memoria no volátil, arrancar y frenar el motor. El menú tendrá un mapa de navegación como se muestra en la figura~\ref{fig:imgPantallasOLED}.

    \begin{figure}[H]
        \centering
            
            \caption{Mapa de navegación del display.}
        \label{fig:imgPantallasOLED}
    \end{figure}

    Se dispondrá de una pantalla splash que por tiempo avanzará a la principal que mostrándonos la frecuencia de trabajo de la salida de potencia, la corriente y tensión del bus de continua, la hora de inicio y fin de funcionamiento de motor y la hora del sistema. Entrando en los menúes pueden editarse las variables de frecuencia, temporales y de seguridad:

    \begin{itemize}
        \item Frecuencia
        \begin{itemize}
            \item Frecuencia de operación
                \begin{itemize}
                \item Es la frecuencia a la cual funcionará el motor cuando llegue a régimen si no hay ninguna entrada de control de velocidad activa.
                \item Mínimo 1$Hz$; Máximo 150$Hz$.
            \end{itemize}
            \item Aceleración
                \begin{itemize}
                \item Es la variación de frecuencia en $\frac{Hz}{S}$ que el motor incrementará en cada segundo hasta llegar a régimen.
                \item Mínimo 1$\frac{Hz}{S}$; Máximo 50$\frac{Hz}{S}$.
            \end{itemize}
            \item Desaceleración
                \begin{itemize}
                \item Es la variación de frecuencia en $\frac{Hz}{S}$ que el motor decrementará en cada segundo hasta llegar a régimen o hasta frenar.
                \item Mínimo 1$\frac{Hz}{S}$; Máximo 50$\frac{Hz}{S}$.
            \end{itemize}
            \item Variación de lineal o cuadrática de las entradas de control
                \begin{itemize}
                \item Es la variación de frecuencia en $Hz$ que las entradas de control de velocidad tendrán entre ellas con 0Hz como valor inicial y la Frecuencia de operación como valor final.
                \item Puede ser lineal o cuadrática.
            \end{itemize}
        \end{itemize}
        \item Seguridad
        \begin{itemize}
            \item Tensión de bus
                \begin{itemize}
                \item Es la mínima tensión en el bus de contínua en $V$ que podrá admitirse sin entrar en estado de emergencia.
                \item Mínimo 250$V$; Máximo 360$V$.
            \end{itemize}
            \item Corriente de bus
                \begin{itemize}
                \item Es la máxima corriente que podrá circular por el bus de contínua en $mA$ sin entrar en estado de emergencia.
                \item Mínimo 500$mA$; Máximo 2000$mA$.
            \end{itemize}
        \end{itemize}
        \item Tiempo
        \begin{itemize}
            \item Hora
                \begin{itemize}
                \item Es la hora del sistema. Se imprime en la parte superior del display.
            \end{itemize}
            \item Inicio
                \begin{itemize}
                \item Es la hora a la que iniciará a funcionar el motor.
                \item Se compara contra la hora de sistema.
            \end{itemize}
            \item Fin
                \begin{itemize}
                \item Es la hora a la que frenará el motor.
                \item Se compara contra la hora de sistema.
            \end{itemize}
        \end{itemize}
    \end{itemize}

\subsubsection{Configuración Wi-Fi}

    El ESP32 genera una red Wi-Fi como access point (AP) que, conectándose a ella, se accede a un formulario WEB que permitirá configurar los mismos parámetros descritos en la sección anterior. Además se podrá encender y apagar el motor desde allí con los parámetros ya guardados. En la figura~\ref{fig:imgWEB} se muestra la interfaz gráfica.
    
    \begin{figure}[H]
        \centering
            
            \caption{Conexionado de display en PCB.}
        \label{fig:imgWEB}
    \end{figure}

    Aún hay mejoras en la experiencia de usuario que se deben realizar desde la interfaz web: Menajes al usuario de validación, redireccionamientos y lectura de datos cargados. Estos cambios deben realizarse desde el código HTML de cada página que se muestra en pantalla, con el agregado de scripts de javascript.

\subsubsection{Memoria no volátil}

    Para el almacenamiento de las variables configuradas por el usuario y mantenerlas cuando el sistema se desenergiza, se optó por utilizar la memoria no volátil del ESP32. Esto evita la necesidad de disponer de un circuito adicional de memoria EEPROM externa. Todos los parámetros arriba mencionados se salvarán utilizando un sector llamado \textit{storage} y las siguientes etiquetas para la lectura y escritura:

    \begin{itemize}
        \item freq\_freq
        \item freq\_acce
        \item freq\_desa
        \item freq\_input
        \item vbus\_min
        \item ibus\_max
        \item hour\_ini
        \item min\_ini
        \item hour\_fin
        \item min\_fin
    \end{itemize}

    Cada vez que el sistema inicia, hace una lectura de todas las variables y las carga en la memoria RAM; luego, en cada edición de parámetros, captura todos los datos editables, los asigna en la memoria RAM del sistema para que entren en vigencia y luego los guarda nuevamente en la memoria no volátil.

\subsubsection{Comunicación SPI}

    Debido a que la exigencia de tiempos del variador de frecuencia es muy alta, no fue posible utilizar un único microcontrolador para el sistema, lo que obligó a disponer de un segundo. El ESP32 se encargará de la operación del HMI: Control de display, lectura de entradas y salidas digitales, salidas analógicas y protecciones de seguridad, además se aprovechó la capacidad de este microcontrolador para agregar la funcionalidad de configuración y comando Wi-Fi; mientras que el STM32 solo se hará cargo del control del variador de frecuencia.

    Una vez que los cambios son realizados en el HMI, estos deben ser enviados al sistema de control del variador de frecuencia. Para ello se utilizó una comunicación SPI entre ambos microcontroladores. El ESP32 actúa como maestro y el STM32 como esclavo.

    Si bien se decidió que el motor pueda estar girando mientras se hacen ediciones de parámetros, estos no impactarán en el variador de frecuencia hasta que el motor se detenga y vuelva a arrancar nuevamente. La máquina de estados del ESP32, es heredada del STM32 ya que se le tuvo que hacer algunos mínimos cambios con motivos funcionales. La misma se encuentra ~\ref{fig:imgMaquinaEstadosHMI}.
 
    \begin{figure}[H]
    \noindent
        \makebox[\textwidth]{
            
        }
        \caption{Máquina de estados del HMI.}
    \label{fig:imgMaquinaEstadosHMI}
    \end{figure}

    La diferencia de esta máquina de estados con la del STM32 es la existencia del estado \textit{SYSTEM\_EMERGENCY\_OK} como intermediario entre \textit{SYSTEM\_EMERGENCY} y \textit{SYSTEM\_IDLE} para asegurar que no se envíe el comando de parada para volver a habilitar el arranque del motor hasta que el sistema tenga todas las condiciones para salir de estado de emergencia

    Para no entorpecer la operación del variador, cada vez que el motor está cambiando de velocidad, la HMI no hará una consulta sistemática de la frecuencia a la que está operando, sino que crea una tarea paralela que hace la cuenta una vez por segundo incrementando o decrementando la frecuencia de operación en la aceleración o desaceleración configurada. Esto ocasiona un ligero desacoplamiento entre el valor de frecuencia que muestra el display y la real, pero es un compromiso que se eligió tener para no afectar la operación del variador.

    Todos estos estados y configuraciones que se cargan sobre el STM32, esclavo, se logran con una comunicación SPI donde el ESP32 es configurado como maestro. Cada una de ellas se realiza enviando un comando, luego de una demora, el maestro le consulta al esclavo la respuesta a la operación enviada inicialmente. La estructura de los mensajes es como muestra la siguiente figura~\ref{fig:imgEstructuraMensajesSPI}.

    \begin{figure}[H]
        \centering
            
            \caption{Estructura de mensajes SPI entre ESP32 y STM32.}
        \label{fig:imgEstructuraMensajesSPI}
    \end{figure}

    En cada transacción el maestro envía el comando, seguido de dos bytes de datos. Cuando el comando no lo requiere, completa esos espacios con ceros. Luego de 400ms, el maestro envía nuevamente un comando, esta vez de lectura de la respuesta, esperando recibir algún estado del motor o un error. Cuando el maestro le pide un dato como la velocidad, dirección, aceleración o desaceleración, el proceso es idéntico con el agregado que el esclavo le responde con el valor solicitado, caso contrario no introduce los dos bytes de datos.

\subsubsection{GPIO - MCP23017}
    \paragraph{\textbf{Descripción general}} El MCP23017 es un expansor de pines de propósito general (GPIO) que se comunica con el microcontrolador a través del bus $I^{2}C$. Proporciona 16 pines de entrada/salida adicionales que pueden ser configurados individualmente como entradas o salidas digitales. En este proyecto, el MCP23017 es utilizado para gestionar las entradas y salidas digitales del HMI, permitiendo la conexión de botones, indicadores LED y otros dispositivos periféricos.

        En esta ocasión, se separó las funcionalidades en dos puertos, dejando al puerto A para varias entradas y salidas aisladas y no aisladas y el puerto B únicamente para una matriz de pulsadores 4x2, como se detallará más adelante y como se grafica en la figura~\ref{fig:MCP23017_SCH}.

        \begin{figure}[H]
            \centering
                
                \caption{Esquema de la matriz de pulsadores.}
            \label{fig:MCP23017_SCH}
        \end{figure}

        Se decidió configurar el expansor con un mapa de memoria secuencial, permitiendo acceder a cada registro del puerto A o B de manera consecutiva. Esto facilitó enormemente el desarrollo de las funciones de lectura y escritura de los registros. Además se utilizó las pines INTA e INTB en forma separada, para distinguir claramente cuando la interrupción se genera por una acción sobre el panel frontal o cuando proviene de una entrada aislada; esto ocurrirá con un estado alto de estos pines.

        Con respecto a las salidas, por disposición del diseño de PCB, se configuraron como salidas activas, permitiendo colocar un estado alto o bajo según se requiera. En el caso de las entradas, se configuraron con resistencias de pull-up internas en el caso de la matriz de pulsadores, evitando la necesidad de colocar unas externas en el diseño; para las entradas aisladas se utilizaron resistencias externas de pull-up y pull-down según el caso para asegurar perfectamente la saturación del optoacoplador.

        \paragraph{Relay} Se dispuso una salida a relay para la externalización de un estado de emergencia. Cada vez que ocurre un consumo excesivo de corriente, una baja tensión en el bus de contínua, una señal externa de emergencia o una temperatura elevada en el circuito de potencia, se activa esta salida la cual estará controlada por el pin GPA1 del MCP23017, como se observa en la figura~\ref{fig:MCP23017_SCH}.

        Se decidió utilizar un optoacoplador para que el consumo de corriente que genera la bobina del relay, quede suministrada por la fuente externa de la HMI, sin cargar las fuentes de tensión descritas en la primera parte de esta sección. Con la utilización del PC817, se diseñó el circuito de la figura~\ref{fig:Relay_SCH}, inicialmente sin el transistor $Q_3$, BC847. Al momento de realizar los cálculos teóricos, se descubrió que el consumo de corriente que la bobina podría demandar, era superior a la que el optoacoplador podría entregar, es por eso que se utilizó una configuración Darlintong final.
        
        \begin{figure}[H]
            \centering
                
                \caption{Esquema de la matriz de pulsadores.}
            \label{fig:Relay_SCH}
        \end{figure}

        Finalmente, la disposición del PCB, queda como se muestra en la figura~\ref{fig:Relay_PCB_2D} y figura~\ref{fig:Relay_PCB_3D}. 

        \begin{figure}[H]
            \centering
                
                \caption{Diseño del control del relay 2D.}
            \label{fig:Relay_PCB_2D}
        \end{figure}

        \begin{figure}[H]
            \centering
                
                \caption{Diseño del control del relay 3D.}
            \label{fig:Relay_PCB_3D}
        \end{figure}

        Además, se puede observar que la bornera de salida queda montada sobre la cara opuesta ya que esto permitirá una mejor disposición final, evitando la interferencia del relay contra el frente de gabinete, sin tener que extender demasiado el PCB. Esto se ve claramente en el render de la figura~\ref{fig:Relay_PCB3D_2}.

        \begin{figure}[H]
            \centering
                
                \caption{Disposición de las borneras con respecto al resto del PCB.}
            \label{fig:Relay_PCB3D_2}
        \end{figure}

        \paragraph{Buzzer} El buzzer será una herramienta que, en caso de haber tenido una pulsada en el panel frontal, se envía un evento a una tarea llamada MCP23017\_buzzer\_control para que el buzzer suene y el usuario entienda que su pulsada fue registrada.

        El diseño es sencillo, como se observa en la figura~\ref{fig:Buzzer_SCH}, donde el pin GPA0 del MCP23017 controla un transistor BC847 que activa el buzzer piezoeléctrico.

        \begin{figure}[H]
            \centering
                
                \caption{Diseño del controlador del buzzer.}
            \label{fig:Buzzer_SCH}
        \end{figure}

        \paragraph{Entradas y salidas aisladas} Se disponen entradas aisladas para el arranque, parada, parada de emergencia, cambio de velocidades del motor y termoswitch interno con el objetivo de brindarle al usuario la posibilidad de conectar un controlador o sensorización externa que pueda interactuar con el variador de frecuencia. Además se coloca una salida analógica de 0-10V que representará la frecuencia de operación, donde 0V será 0Hz y 10V será 150Hz.

        Cada una de estas entradas y salidas son aisladas con un optoacoplador para evitar que ruidos o picos de tensión puedan dañar los componentes internos del HMI. See diseñó un circuito para los controles de motor como los de la figura~\ref{fig:Input_SCH}, un circuito para la salida analógica como figura~\ref{fig:Output_SCH} y un circuito para la entrada del termoswitch como figura~\ref{fig:Thermoswitch_SCH}.

        \begin{figure}[H]
            \centering
                
                \caption{Diseño del controlador de entradas aisladas.}
            \label{fig:Input_SCH}
        \end{figure}

        \begin{figure}[H]
            \centering
                
                \caption{Diseño del controlador de salida analógica aislada.}
            \label{fig:Output_SCH}
        \end{figure}

        \begin{figure}[H]
            \centering
                
                \caption{Diseño del controlador de entrada del termoswitch aislada.}
            \label{fig:Thermoswitch_SCH}
        \end{figure}

        Finalmente, la disposición del PCB, queda como se muestra en la figura~\ref{fig:ISO_IO_PCB} y figura~\ref{fig:ISO_IO_PCB3D} donde se pueden observar claramente la línea de optoacopladores y los dos planos de tensión aislados entre si.

        \begin{figure}[H]
            \centering
                
                \caption{Diseño del controlador de entradas y salidas aisladas PCB.}
            \label{fig:ISO_IO_PCB}
        \end{figure}

        \begin{figure}[H]
            \centering
                
                \caption{Diseño 3D del controlador de entradas y salidas aisladas PCB.}
            \label{fig:ISO_IO_PCB3D}
        \end{figure}

        De la misma manera que el relay, las borneras de entrada y salida quedan montadas sobre la cara opuesta.

        El funcionamiento de la salida 0-10V parte de una señal PWM 3.3Vdc máximo generada por el microcontrolador, amplificada por el transistor 2N7002 (Q2), filtrada por el capacitor C22 para excitar al transistor BC847 (Q1) que controlará el led del optoacoplador. Finalmente, con un último filtro pasivo (C21) se obtiene la señal analógica de 0-10Vdc sobre la resistencia de carga R22. Este circuito fue simulado en LTSpice para certificar su correcto funcionamiento, como se observa en la figura~\ref{fig:ISO_0-10V_SIM} y figura~\ref{fig:ISO_0-10V_signal_output}.

        \begin{figure}[H]
            \centering
                
                \caption{Simulación del controlador de salida analógica aislada.}
            \label{fig:ISO_0-10V_SIM}
        \end{figure}

        \begin{figure}[H]
            \centering
                
                \caption{Gráficos de tensión de salida 0-10V.}
            \label{fig:ISO_0-10V_signal_output}
        \end{figure}

        El detalle importante a tener en cuenta es la corriente que circula por la resistencia R21 que nos obliga a utilizar una resistencia de 1W ya que la disipación de potencia en la misma es de aproximadamente 0,75W.

        \paragraph{Botonera}

        Para el panel frontal se dispondrá una matriz de pulsadores de 4x2, donde cada fila y columna se conectarán al MCP23017, quien será el encargado de la lectura de las pulsada. Estos eventos serán reportados como una interrupción del expansor de GPIO y se reportará al ESP32, en donde se hará la lectura de los puertos y determinación del estado de los pulsadores. En el diseño original se dispuso de dos resistencias de pull-up, una por cada fila, sin embargo no fueron montadas y se configuró las salidas del controlador de pines de esa misma manera, generando un ahorro en la disposición de las resistencias R26 y R27, algo que podrá observarse en la figura~\ref{fig:MatrizPulsadores_SCH}.
        
        \begin{figure}[H]
            \centering
                
                \caption{Esquema de la matriz de pulsadores.}
            \label{fig:MatrizPulsadores_SCH}
        \end{figure}

        Inicialmente la placa de la HMI fue pensada con la botonera montada sobre la misma PCB, pero por cuestiones de diseño del gabinete final, se dispuso que quede en una placa diferente, con un conector que comunique ambas placas. El diseño de la PCB de la botonera es el que se muestra en la figura~\ref{fig:MatrizPulsadoresPCB2D} y figura~\ref{fig:MatrizPulsadoresPCB3D}.

        \begin{figure}[H]
            \centering
                
                \caption{Diseño PCB de la botonera.}
            \label{fig:MatrizPulsadoresPCB2D}
        \end{figure}

        \begin{figure}[H]
            \centering
                
                \caption{Diseño 3D de la botonera.}
            \label{fig:MatrizPulsadoresPCB3D}
        \end{figure}

        Al momento de pulsar un botón, el MCP23017 generará un interrupción por el pin INTB, leído por el ESP32 y generando una interrupción. La tarea \textit{GPIO\_interrupt\_attendance\_task} recibe el tipo de evento, interpreta su origen y se envía a si mismo otro evento con el tipo de botón presionado. Luego de 50mS de anti rebote, se lee nuevamente el estado de los pines para certificar que el estado de las entradas se mantenga en la misma condición y se envía el evento final a la cola de eventos del display o sistema según corresponda.

        El control de las salidas de la matriz de pulsadores está a cargo de una tarea local llamada \textit{MCP23017\_keyboard\_control} que alterna el estado alto en las dos filas de la matriz, excepto cuando registra que alguna de las columnas está en estado bajo, signo que delata que hay un botón pulsado. Esta tarea no toma ninguna decisión sobre la lectura, para eso está la \textit{GPIO\_interrupt\_attendance\_task} mencionada anteriormente.

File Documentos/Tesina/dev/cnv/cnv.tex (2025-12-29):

\label{sec:3_dev_cnv}
\subsection{Conversor DC-DC}
\subsubsection{Selección de topología}

El módulo conversor debe:
\begin{itemize}
    \item Elevar de 12Vdc a 320Vdc,
    \item mantener una tensión de salida estable frente a variación de carga,
    \item ofrecer un arranque suave para no exigir en exceso a los componentes, 
    \item y permitir desactivar el bus dc.
\end{itemize} 

Para cumplir con estos requerimientos se implementó una topología de conversor aislado en configuración pushpull. 

Esta topología fue seleccionada por su adecuada capacidad de manejo de potencia para el tipo de carga prevista y por su ventaja de permitir una elevada relación entre la tensión de entrada y la de salida. A diferencia de la topología flyback, el convertidor push-pull transfiere energía durante ambos semiciclos del ciclo de conmutación, optimizando así la utilización del núcleo del transformador. Si bien requiere transistores capaces de soportar el doble de la tensión de entrada y un transformador con derivación central y, aunque el convertidor en puente completo ofrece una mayor eficiencia y menor generación de calor, el push-pull presenta una construcción más simple y un menor costo al necesitar menos componentes.

Otra ventaja importante de esta topología es que, como se puede aplicar toda la tensión de entrada al primario en cada ciclo, permite el uso de transformadores con menor relación de espiras, simplificando el diseño magnético, reduciendo pérdidas por histéresis y permitiendo operar a frecuencias de conmutación más altas. Esto último, además, posibilita el uso de inductores y capacitores de menor tamaño.

El aislamiento galvánico que brinda el transformador permite formar una barrera entre el bus de alta tensión y el de baja tensión, lo que se traduce a una mayor seguridad tanto en instalación y funcionamiento, como en el ensayo para el operario. Además, esto habilitó un diseño más seguro y modular, facilitando la integración del conversor con otros subsistemas como el del control general.

\subsubsection{Requerimientos mínimos eléctricos}

Se establecieron los requerimientos mínimos que el convertidor debe cumplir, a partir de los cuales se realizaron los cálculos de diseño. Los parámetros principales se resumen a continuación:

\begin{table}[h!]
\centering
\renewcommand{\arraystretch}{1.2}
\begin{tabular}{|l|c|}
\hline
\textbf{Parámetro} & \textbf{Valor} \\
\hline
Frecuencia ($f$) & 50 kHz \\
Tensión entrada ($V_{in}$) & 12 V \\
Tensión salida ($V_{out}$) & 320 V \\
Potencia salida ($P_{out}$) & 400 W \\
Rendimiento ($\eta$) & 0,8 \\
\hline
\end{tabular}
\caption{Requerimientos mínimos}
\end{table}

Con estos valores, y asumiendo un ciclo de trabajo suficientemente elevado para considerar la corriente de entrada como continua, se obtienen las siguientes expresiones:

\[
I_{in}=\frac{P_{out}}{V_{in} \ \eta}  
\]
\[
I_{out}=\frac{P_{out}}{V_{out}} 
\]

\begin{table}[h!]
\centering
\renewcommand{\arraystretch}{1.2}
\begin{tabular}{|l|c|}
\hline
\textbf{Corrientes} & \textbf{Valor [A]} \\
\hline
Entrada & 37.04 \\
Salida & 1.25 \\
\hline
\end{tabular}
\caption{Valores calculados de corrientes}
\end{table}

\subsubsection{Diseño de transformador}

\paragraph{Selección del núcleo}
Se seleccionó un núcleo de ferrita ETD36 debido a su geometría optimizada para aplicaciones de conmutación y su facilidad de montaje. Este modelo ofrece un equilibrio adecuado entre la capacidad para manejar el flujo magnético y minimizar pérdidas, evitando la saturación bajo las condiciones de diseño. Además, su tamaño compacto y buena disipación térmica lo hacen apropiado para la potencia prevista.

A continuación, en la tabla~\ref{tab:cnv_caracteristicas_ETD36} se listan sus características más importantes, junto a sus características magnéticas en la tabla~\ref{tab:cnv_EDT36_Caracteristicas_magneticas} y sus dimensiones físicas en la tabla~\ref{tab:cnv_EDT36_Dimensiones_Fisicas} para el cálculo posterior.

En la figura~\ref{fig:cnv_EDT36_referencias_medidas} se pueden ver referencias de las medidas descriptas.
\begin{table}[H]
\centering
\renewcommand{\arraystretch}{1.2}
\begin{tabular}{|l|l|}
\hline
\textbf{Parámetro} & \textbf{Valor} \\
\hline
Aleación & MgZn \\
Forma & ETD36 \\
Material & GP95 \\
Color & Negro \\
\hline
\end{tabular}
\caption{Información general del núcleo ETD36}
\label{tab:cnv_caracteristicas_ETD36}
\end{table}

\begin{table}[H]
\centering
\renewcommand{\arraystretch}{1.2}
\begin{tabular}{|l|l|}
\hline
\textbf{Parámetro} & \textbf{Valor} \\
\hline
$B_{sat}$ & 400 mT \\
$\mu_i$ (25°C) & 3300 \\
\hline
\end{tabular}
\caption{Características magnéticas del núcleo ETD36}
\label{tab:cnv_EDT36_Caracteristicas_magneticas}
\end{table}

\begin{table}[H]
\centering
\renewcommand{\arraystretch}{1.2}
\begin{tabular}{|l|l|}
\hline
\textbf{Parámetro} & \textbf{Valor} \\
\hline
Largo efectivo $l_e$ & 97.5 mm \\
Área transversal $A_c$ & 70.88 mm$^2$ \\
Área ventana $A_w$ & 231 mm$^2$ \\
Volumen efectivo $V_e$ & 20757 mm$^3$ \\
Dimensión A & 36 mm \\
Dimensión B & 26 mm \\
Dimensión C & 21.5 mm \\
Dimensión D & 14 mm \\
Dimensión E & 9.5 mm \\
Dimensión F & 11.2 mm \\
\hline
\end{tabular}
\caption{Parámetros geométricos y efectivos del núcleo ETD36}
\label{tab:cnv_EDT36_Dimensiones_Fisicas}
\end{table}

\begin{figure}[h!tbp]
\centering
    
    \caption{Referencias de medidas del transformador.}
\label{fig:cnv_EDT36_referencias_medidas}
\end{figure}

\paragraph{Relación de transformación y cálculo de espiras}

El cálculo inicial de la relación de transformación arrojó un valor de 1:26.6, sin embargo, tras las pruebas experimentales, se incorporó un margen de seguridad para aumentarla dado que a máxima carga la tensión del secundario tiende a disminuir. Para mantener la tensión dentro del rango admisible del bus de continua, se incrementó la relación a 1:45, equivalente a un factor de 1.7. 

El devanado primario se compone de 3 + 3 espiras con punto medio, y el secundario consta de 135 espiras.

\paragraph{Sección de conductores}

Para la elección de la sección del conductor se adoptaron densidades de corriente típicas de 2 a 5 $A/mm^2$, valores comunes en bobinados de transformadores. En el primario se seleccionó una densidad de 3 $A/mm^2$ y en el secundario de 5 $A/mm^2$, considerando la cantidad de espiras necesarias.

Suponiendo una forma de onda cuadrada con ciclo de trabajo del 45\%, la corriente RMS del primario resulta 13.8 $A$, lo que determina secciones de 4.6 $mm^2$ para el primario y 0.3 $mm^2$ para el secundario. Finalmente, se utilizaron conductores de 5 $mm^2$ en el primario y doble alambre de 0.4 $mm$ de diámetro en el secundario. No se verifica la ocupación de la ventana del núcleo por lo que se incrementa la densidad de corriente del secundario a $10A/mm^2$ y se bobina con un solo alambre de 0.4 $mm$ de diámetro.

\begin{figure}[H]
\centering
    
    \caption{Imagen de transformador del conversor.}
\label{fig:imgDevTrafo}
\end{figure}

\subsubsection{Diseño y simulación de circuito de conmutación}
El circuito de conmutación del conversor debe manejar corrientes elevadas, por lo que la selección de los transistores de potencia y del circuito de excitación de compuerta es crítica. En la figura~\ref{fig:imgDevEsqPushPull} se muestra el diagrama circuital simplificado del convertidor.

\begin{figure}[H]
\centering
    
    \caption{Diagrama simplificado del conversor push pull.}
\label{fig:imgDevEsqPushPull}
\end{figure}

La topología utilizada corresponde a una fuente push-pull, la cual emplea dos transistores que conmutan de forma complementaria. A la salida se dispone un rectificador de onda completa con filtro LC que estabiliza la tensión de salida. Se incorpora además un diodo en serie para evitar el frenado regenerativo y proteger el capacitor principal frente a sobrecargas\footcite{DisenoDeRectificadoresRegenerativos_Velaquez}.

Con el fin de reducir la corriente en cada dispositivo, se implementaron dos transistores en paralelo, lo que permitió distribuir mejor la disipación térmica y disminuir la resistencia de conducción efectiva. Este método reduce las pérdidas y mejora la eficiencia global del sistema.

Un aspecto fundamental para garantizar la vida útil y el correcto funcionamiento de los transistores es asegurar una adecuada refrigeración. La disipación térmica resulta crítica para evitar el sobrecalentamiento y preservar la integridad de los dispositivos. Este criterio constituyó el punto de partida para el diseño del montaje.

\paragraph{Selección de los transistores de conmutación}

La corriente máxima por rama alcanza aproximadamente $37 A$, valor adecuado para el uso de transistores MOSFET. Los dispositivos deben soportar una tensión drenaje-fuente superior a $24 V$ y presentar una resistencia $R_{DS(on)}$ lo más baja posible para minimizar pérdidas. Dado que la frecuencia de operación es de $50 kHz$, se seleccionó el IRFB4110 de International Rectifier, cuyas características se muestran en la tabla~\ref{tab:IRFB4110_specs}.

\begin{table}[H]
\centering
\renewcommand{\arraystretch}{1.3} % Aumenta el espaciado para mejor legibilidad
\begin{tabular}{|l|l|}
\hline
\multicolumn{2}{|c|}{\textbf{Características Clave del MOSFET IRFB4110}} \\
\hline
\textbf{Parámetro} & \textbf{Valor Típico / Máximo} \\
\hline
Tipo de Transistor & N-Channel HEXFET \\
Tensión Máxima Drenaje-Fuente ($V_{DSS}$) & 100 V \\
Corriente Continua Máx. Drenaje ($I_D$ @ 25°C) & 120 A \\
Resistencia Drenaje-Fuente On ($R_{DS(on)}$ máx.) & $3.7 \, m\Omega$ \\
Disipación de Potencia Máx. ($P_D$ @ 25°C) & 370 W \\
Carga de Puerta Total ($Q_g$) & 150 nC \\
Encapsulado & TO-220AB \\
\hline
\end{tabular}
\caption{Especificaciones técnicas principales del MOSFET de potencia IRFB4110.}
\label{tab:IRFB4110_specs}
\end{table}

De acuerdo con la curva de área de operación segura, el dispositivo trabaja dentro de condiciones seguras, considerando pulsos de $20 \mu s$ y tensión de $24 V$, muy por debajo de sus límites máximos.

\begin{figure}[H]
\centering
    
    \caption{Área de operación segura del IRFB4110.}
\label{fig:imgDevSOA-IRFB4110}
\end{figure}

\paragraph{Simulación del circuito de conmutación}

Para anticipar y evaluar el diseño del circuito se utilizó la herramienta LTSpice para la simulación, algo que se muestra en la figura ~\ref{fig:imgDev_EsqSimSimplificado}. Solo se buscó analizar el comportamiento tanto del transformador como de los transistores de potencia y la etapa de filtrado. Se excluyó el circuito de control por la complejidad. En este se colocó el transformador con sus tres arrollamientos con un acoplamiento unitario además de los componentes complementarios. 

Para asegurar un buen funcionamiento del conversor en las simulaciones se exigió ligeramente al circuito, colocando una carga que consuma $400W$ para generar corrientes más grandes sobre los transistores.

\begin{figure}[H]
\centering
    
    \caption{Esquema circuital del conversor para simulación.}
\label{fig:imgDev_EsqSimSimplificado}
\end{figure}

Se inyectaron dos señales a las compuertas de los transistores de $0V$ a $12V$ con un ciclo de actividad de $45\%$ y una frecuencia de $50 kHz$ con la de la figura ~\ref{fig:imgDev_SimVgs}.

\begin{figure}[H]
\centering
    
    \caption{Simulación de las tensiones de compuerta a fuente de ambos transistores.}
\label{fig:imgDev_SimVgs}
\end{figure}

Por un lado, se obtuvo la tensión entre drenaje y fuente, la cual desciende a $0V$ cuando el transistor conduce y a $24V$ (el doble de la tensión de fuente) cuando deja de hacerlo, lo esperado en una topología push-pull. Por otro lado, en la figura~\ref{fig:imgDev_SimVds} se muestra el arranque del sistema.

\begin{figure}[H]
\centering
    
    \caption{Simulacion de tension entre drain y source de un transistor de entrada.}
\label{fig:imgDev_SimVds}
\end{figure}

A continuación, en la figura ~\ref{fig:imgDev_SimVds-Ids} se gráfica la corriente de drenaje de uno de los transistores de entrada. Se nota una gran corriente de entrada al inicio debido a la carga inicial del capacitor además de encontrarse el circuito cargado, escenario que no podrá ocurrir en nuestro sistema. Esta corriente de entrada es demasiado alta incluso para la carga del capacitor, por ello se implementa el circuito de arranque suave sobre el sistema de control. 

\begin{figure}[H]
\centering
    
    \caption{Simulación de tensión entre drenaje y fuente en trazo verde y corriente de drenaje en trazo azul.}
\label{fig:imgDev_SimVds-Ids}
\end{figure}

En los transitorios de la figura~\ref{fig:imgDev_SimIds} se nota una corriente cuadrada con un ciclo de trabajo de $45\%$ con una corriente pico de $40 A$.

\begin{figure}[H]
\centering
    
    \caption{Simulación de corriente de drenaje en el permanente.}
\label{fig:imgDev_SimIds}
\end{figure}

Por otro lado, en la figura~\ref{fig:imgDev_SimVout-Iout}, tenemos la tensión y la corriente sobre la carga, además de notarse la carga del capacitor en el arranque del convertidor.

\begin{figure}[H]
\centering
    
    \caption{Simulación de tensión sobre la carga en trazo verde y la corriente en la carga en trazo azul.}
\label{fig:imgDev_SimVout-Iout}
\end{figure}

\paragraph{Diseño del controlador de los transistores de conmutación}

Para lograr conmutaciones rápidas y minimizar pérdidas por transición, se diseñó un circuito totem-pole driver como el de la figura ~\ref{fig:imgDev_EsqTotemPole} encargado de excitar las compuertas de los MOSFETs. Dado que la compuerta se comporta como una carga capacitiva, es necesario conmutarla rápidamente entre $0V$ y $12V$.

El circuito totem-pole proporciona una respuesta veloz con bajo consumo. Se estimó una corriente de colector de aproximadamente $1.2A$, calculada en la ecuación~\eqref{eq:dev_cnv_IcTotemPol}.
  \begin{equation}\label{eq:dev_cnv_IcTotemPol}
  I_c=\frac{V_{CC}}{R_g} \cong 1.2A
  \end{equation}

Para su implementación se utilizaron transistores SS8050 (NPN) y SS8550 (PNP), ambos con una corriente máxima admisible de $1.5 A$.

\begin{figure}[H]
\centering
    
    \caption{Esquema de controlador totem-pole.}
\label{fig:imgDev_EsqTotemPole}
\end{figure}

Se realizan simulaciones del circuito en \textit{LTspice} representado en la figura~\ref{fig:imgDev_EsqSim_TotemPole} con el objetivo de evaluar los tiempos de transición asociados al accionamiento del transistor MOSFET mediante la etapa \textit{totem-pole}. Este análisis permite verificar que la compuerta del dispositivo alcance los niveles de tensión requeridos dentro de los tiempos adecuados para garantizar una conmutación segura y eficiente, algo que en la figura ~\ref{fig:imgDev_Conv_SimVgate}.

\begin{figure}[H]
\centering
    
    \caption{Esquema circuital del circuito totem-pole para simulación.}
\label{fig:imgDev_EsqSim_TotemPole}
\end{figure}

En el circuito se aplica una señal cuadrada de $50kHz$ y se registra la tensión en la compuerta del MOSFET para evaluar la respuesta dinámica de la etapa de manejo.

\begin{figure}[H]
\centering
    
    \caption{Simulación de la tensión de control y la tensión en la compuerta del MOSFET.}
\label{fig:imgDev_Conv_SimVgate}
\end{figure}

Mediante una ampliación de las zonas de conmutación se determina un tiempo de subida de $345ns$ y un tiempo de bajada de $369.83ns$. Estos valores graficados en la figura~\ref{fig:imgDev_Conv_SimRiseTime} y ~\ref{fig:imgDev_Conv_SimFallTime} se consideran adecuados para la frecuencia de operación seleccionada y confirman que el circuito presenta capacidades suficiente para conmutar la compuerta.

\begin{figure}[H]
\centering
    
    \caption{Simulación del tiempo de subida de la tensión de compuerta frente a la señal de control.}
\label{fig:imgDev_Conv_SimRiseTime}
\end{figure}

\begin{figure}[H]
\centering
    
    \caption{Simulación del tiempo de bajada de la tensión de compuerta frente a la señal de control.}
\label{fig:imgDev_Conv_SimFallTime}
\end{figure}

\subsubsection{Diseño de circuito de control}

Para el control del convertidor se empleó el TL494, un circuito integrado ampliamente utilizado en fuentes conmutadas por su robustez y versatilidad. Este dispositivo integra un oscilador, amplificadores de error, comparadores y salidas PWM, permitiendo una regulación precisa de la tensión de salida.

El circuito fue configurado de modo tal que, al detectar variaciones en la tensión de salida respecto al valor de referencia, ajusta el ciclo de trabajo de los transistores de potencia para mantener estable la salida ante cambios en carga o en tensión de entrada. Con lo componente $C_1$ y $R_1$, gracias a las ecuaciones del fabricante, se fijó la frecuencia de conmutación en $50 kHz$, valor que representa un compromiso adecuado entre rendimiento y pérdidas. 

\begin{figure}[H]
\centering
    
    \caption{Esquema de circuito de control del conversor basado en el TL494.}
\label{fig:imgDev_EsqTL494}
\end{figure}

En la figura~\ref{fig:imgDev_EsqTL494Comp} se detalla el agregado del potenciómetro $R_5$ para el ajuste fino en el lazo de realimentación para compensar posibles dispersiones entre componentes y fijar con precisión la tensión del bus de continua. Además, se añadió un circuito $R_4 C_2$ de arranque suave (soft-start) que permiten limitar la corriente de irrupción inicial y proteger los componentes durante el encendido.

\begin{figure}[H]
\centering
    
    \caption{Esquema de circuitos complementarios para ajuste y arranque suave.}
\label{fig:imgDev_EsqTL494Comp}
\end{figure}

\paragraph{Circuito de medición de tensión}

El conversor es completamente aislado galvánicamente, lo que mejora la seguridad y facilita las pruebas del sistema. Para realizar las mediciones de tensión y corriente de forma aislada, se implementó un optoacoplador PC817 en conjunto con un compensador TL431 como lo representa la figura~\ref{fig:imgDev_EsqTL431-PC817}, los cuales atenúan las altas frecuencias no deseadas, garantizan una realimentación estable del bus DC y protección contra transitorios\footcite{TL431_ONSEMI}.

\begin{figure}[H]
\centering
    
    \caption{Esquemático de circuito de medición de tensión aislado usando un PC817 y TL431.}
\label{fig:imgDev_EsqTL431-PC817}
\end{figure}

\paragraph{Circuito de medición de corriente}

En la medición de corriente se utiliza el integrado \textit{ACS712}, un sensor basado en efecto Hall con salida lineal y aislamiento galvánico completo. Este dispositivo de la figura~\ref{fig:imgDev_EsqACS712} se alimenta con $5V$ y permite medir corrientes de hasta $\pm 5A$, valor adecuado para los niveles de corriente presentes en nuestro sistema. La salida del sensor entrega $2.5V$ para una corriente de $0A$. Dado que la electrónica de adquisición opera a $3.3V$, y con el fin de evitar posibles sobre-tensiones en la etapa de lectura, se invierte el sentido de circulación de la corriente de modo que el rango útil del sensor se mantenga entre $0V$ y $2.5V$, garantizando así un funcionamiento seguro y dentro de las especificaciones del sistema.

\begin{figure}[H]
\centering
    
    \caption{Esquemático de circuito de medición de corriente usando un ACS712.}
\label{fig:imgDev_EsqACS712}
\end{figure}

\subsubsection{Diseño de circuito impreso}

El diseño de la PCB del conversor presenta una mayor complejidad en comparación con otras etapas del sistema, debido a la coexistencia de corrientes elevadas y la necesidad de garantizar una adecuada aislación entre las distintas secciones del circuito.

En la figura \ref{fig:imgDev_cnv_PCB_Front1} se muestra la parte inferior de la cara frontal de la placa. En el sector izquierdo se ubican las entradas de potencia, junto con los capacitores asociados y las pistas que conducen la energía hacia el transformador. Todas las pistas correspondientes a la etapa de potencia se dejaron sin recubrimiento de máscara antisoldante, de manera de permitir su estañado y así incrementar la sección transversal efectiva del conductor, reduciendo la caída de tensión y las pérdidas por conducción.

En la zona central de esta cara se encuentra el integrado TL494, encargado de generar las dos señales de control utilizadas para la conmutación de los transistores de potencia de la etapa push-pull. Hacia la derecha se dispone la etapa de salida del conversor, conformada por el puente rectificador, la bobina de filtrado y el capacitor de salida. Los transistores del rectificador se encuentran montados en la cara posterior de la placa, optimizando la distribución térmica y el aprovechamiento del espacio.

\begin{figure}[H]
\centering
    
    \caption{Vista frontal de la parte inferior de la PCB del conversor.}
\label{fig:imgDev_cnv_PCB_Front1}
\end{figure}

En la parte superior de la cara frontal, mostrada en la figura \ref{fig:imgDev_cnv_PCB_Front2}, se localiza a la izquierda el circuito de disparo de los transistores de potencia, mientras que a la derecha se encuentra el transformador de alta frecuencia.

\begin{figure}[H]
\centering
    
    \caption{Vista frontal de la parte superior de la PCB del conversor.}
\label{fig:imgDev_cnv_PCB_Front2}
\end{figure}

Finalmente, en la cara posterior de la PCB, figura \ref{fig:imgDev_cnv_PCB_Back}, se observan los transistores y diodos de potencia, así como los circuitos de medición de tensión y corriente ubicados en la zona central de la placa.

\begin{figure}[H]
\centering
    
    \caption{Vista frontal de la parte superior de la PCB del conversor.}
\label{fig:imgDev_cnv_PCB_Back}
\end{figure}

\subsubsection{Limitaciones detectadas en la implementación}

La etapa conversora no es capaz de entregar de forma continua una potencia del orden de $1/3\text{HP}$. Esta limitación se origina en un error de cálculo en la densidad de corriente del devanado secundario del transformador. La corriente por unidad de área resulta excesiva, generando temperaturas superiores a la admitida por los aislantes y el núcleo. Como consecuencia, el sistema queda limitado a una potencia continua aproximada de $1/6,\text{HP}$.

La medición de tensión no arrojó resultados satisfactorios debido a que la relación entre la tensión del bus DC y la tensión de salida no es lineal, sino de tipo cuadrática, presentando además una compresión en la zona de interés. Esto provoca una baja resolución efectiva de la medición. Esta característica se debe al comportamiento no lineal del optoacoplador PC817. Adicionalmente, la tensión de salida en el punto nominal de operación es de aproximadamente $3.15,V$, valor que no resulta adecuado para el convertidor analógico-digital (ADC) del ESP32, ya que se encuentra fuera de su rango óptimo de resolución, impidiendo discriminar correctamente pequeñas variaciones de tensión.

Por su parte, la medición de corriente mediante el sensor ACS712 tampoco presentó un desempeño adecuado, principalmente debido a la elevada dispersión en la tensión de salida, lo que introduce incertidumbre y ruido en la medición. Esta característica limita su utilidad para la aplicación desarrollada.

Finalmente, se identificó la ausencia de filtrado pasivo adecuado en las etapas de medición como un factor adicional que degradó la calidad de las señales adquiridas. En particular, la presencia de picos de tensión generaba lecturas erróneas visualizadas en la interfaz HMI. Para mitigar este efecto, se implementaron filtros RC pasivos, mejorando la estabilidad y confiabilidad de las mediciones. 

\subsubsection{Dificultades encontradas}

En esta sección se detallan las complicaciones enfrentadas durante el diseño del conversor y las soluciones aplicadas, dado que este resultó ser el componente de potencia más complejo del proyecto. En esta etapa inicial se contaba con un conocimiento limitado sobre el diseño de convertidores de alta potencia, por lo que comprender los aspectos críticos implicó un proceso prolongado de análisis y pruebas.

La idea inicial fue implementar una topología de puente completo, ya que presenta una alta eficiencia y era un aspecto que considerábamos prioritario. Para ello se fabricó el transformador de la figura~\ref{fig:imgDev_Dif_Trafo1} con un núcleo cuya relación de transformación era de $12:320$. El tamaño del núcleo resultó ser considerablemente grande, lo que obligó a bobinar un primario de 16 espiras, generando pérdidas significativas. El número de vueltas había sido calculado correctamente según las expresiones presentadas en el marco teórico, pero en la práctica el diseño no ofreció el rendimiento esperado.

\begin{figure}[H]
\centering
    
    \caption{Imagen de transformador midiendo la inductancia del primario.}
\label{fig:imgDev_Dif_Trafo1}
\end{figure}

En los ensayos se logró obtener únicamente $30 W$ con una eficiencia del $50\%$, un valor demasiado bajo para los objetivos del diseño. Parte de este desempeño deficiente se debía a que, en esta primera iteración, no habíamos dimensionado correctamente la corriente requerida en el primario, además de que existían pérdidas considerables en el cableado del bus DC de baja tensión debido al montaje realizado de la figura~\ref{fig:imgDev_Dif_PuenteHTrafo1}.

\begin{figure}[H]
\centering
    
    \caption{Imagen de transformador 1 con puente H.}
\label{fig:imgDev_Dif_PuenteHTrafo1}
\end{figure}

Al observar la baja performance de este transformador y tomando como referencia el diseño de transformadores de fuentes conmutadas existentes, además de otras guías prácticas, se construyó un segundo transformador con 3 vueltas en el primario y, como ilustra la figura~\ref{fig:imgDev_Dif_PuenteHTrafo2}, se redujo drásticamente la distancia del cableado del bus DC. Estos cambios produjeron una mejora sustancial.

\begin{figure}[H]
\centering
    
    \caption{Imagen de transformador 2 con puente H.}
\label{fig:imgDev_Dif_PuenteHTrafo2}
\end{figure}

Con el objetivo de optimizar aún más el rendimiento, se construyó el tercer transformador de la figura ~\ref{fig:imgDev_Dif_PuenteHTrafo3}. En este caso no disponíamos del carrete adecuado, por lo que fue impreso en plástico y luego bobinado manualmente.

\begin{figure}[H]
\centering
    
    \caption{Imagen de transformador 3 con puente H.}
\label{fig:imgDev_Dif_PuenteHTrafo3}
\end{figure}

Este tercer transformador presentó la mejor performance: con una carga de $250\Omega$ se obtuvo una tensión máxima de $297V$ y una corriente de $1.2A$. Sin embargo, persistía un problema importante: no era posible alcanzar la tensión objetivo de $320V$.

Ante esta situación, se decidió cambiar a una topología más simple. Esto respondía tanto a la necesidad de reducir la complejidad del circuito de conmutación como a la de simplificar el cableado. Además, los transistores se dañaban con frecuencia durante las pruebas y solían fallar de a pares, lo cual implicaba un considerable gasto de tiempo y reemplazo de componentes.

La topología seleccionada fue la de \textit{push-pull}. Como se observa en la figura~\ref{fig:imgDev_Dif_Pushpull}, se montaron tres transistores por cada rama, colocados en un disipador y aislados mediante mica.

\begin{figure}[H]
\centering
    
    \caption{Imagen de transistores en topologia Push Pull.}
\label{fig:imgDev_Dif_Pushpull}
\end{figure}

A continuación, en la figura~\ref{fig:imgDev_Dif_PushpullEtapa2}, con esta nueva topología se obtuvo un rendimiento levemente inferior, pero las ventajas en simplicidad y confiabilidad justificaron su adopción. Durante sus ensayos se detectó que la tensión en los terminales del transformador no coincidía con la tensión real entregada por la fuente, debido a caídas en los conductores. Esto explicaba por qué no se alcanzaban los $320V$. En un primer intento se incrementó significativamente la sección de los cables, incluso utilizando barras de aluminio. Si bien esto no mejoró los resultados, permitió observar la ventaja de evitar el uso de mica en los transistores, reemplazándolo por dos bloques de disipadores independientes, lo que mejoró notablemente la disipación y prolongó la vida útil de los transistores. También se ensayó el uso de los dos mejores transformadores, tanto con los primarios en paralelo como en serie, sin obtener mejoras sustanciales.

\begin{figure}[H]
\centering
    
    \caption{Imagen de conversor pushpull con barras de aluminio y transformadores en paralelo.}
\label{fig:imgDev_Dif_PushpullEtapa2}
\end{figure}

Finalmente, en la figura ~\ref{fig:imgDev_Dif_PushpullEtapa3} se muestra que, utilizando el transformador con mejor rendimiento, se decidió incrementar la relación de transformación agregando espiras en el secundario por encima del valor inicial de $12:320$. Paralelamente se implementó un circuito de control práctico con el TL494, permitiendo ajustar el ciclo de trabajo mediante un potenciómetro. Esta modificación sí permitió alcanzar los $320V$ y obtener momentáneamente una potencia de salida de 460 W. Sin embargo, surgió un inconveniente importante: sin carga, la tensión escalaba fácilmente por encima de los $450V$. Esto hizo indispensable implementar un control realimentado, utilizando una medición aislada de la tensión de salida.

\begin{figure}[H]
\centering
    
    \caption{Imagen de conversor pushpull realimentado con TL494 y placa de medicion.}
\label{fig:imgDev_Dif_PushpullEtapa3}
\end{figure}

Por cuestiones de espacio y dado que el transformador más eficiente contaba con un carrete impreso en plástico, finalmente se optó por utilizar el segundo mejor transformador, ligeramente más compacto. Si bien la topología push-pull no ofrece la mayor eficiencia posible, proporciona una implementación más simple y confiable, a costa de requerir un primario con punto medio, lo cual resulta mucho menos problemático que gestionar ocho transistores como en el puente completo.

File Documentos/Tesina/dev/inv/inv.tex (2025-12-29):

\label{sec:3_dev_inv}
\subsection{Inversor}

\subsubsection{Introducción}

En esta sección se describe el diseño y funcionamiento de la etapa inversora, encargada de convertir la tensión continua del bus DC en una tensión alterna trifásica apta para la alimentación del motor. Para esta etapa se adoptó una topología de puente completo trifásico, basada en seis interruptores electrónicos de potencia, la cual se caracteriza por su simplicidad, versatilidad y amplia utilización en variadores de frecuencia.

Esta configuración permite generar tensiones de polaridad bidireccional en cada fase, resultando adecuada para el manejo de cargas inductivas y para la implementación de estrategias de modulación como el vector espacial (SVM). Si bien existen topologías que pueden ofrecer una menor distorsión armónica en la tensión de salida, la topología seleccionada resulta suficiente para los niveles de potencia y exigencias de la aplicación desarrollada, sin comprometer el correcto funcionamiento del motor.

Por otro lado, se priorizó el cumplimiento de la aislación galvánica entre la etapa de control y la etapa de potencia, con el objetivo de proteger al microcontrolador frente al ruido eléctrico generado durante las conmutaciones de los transistores. Para ello se emplearon dispositivos de aislamiento en las señales de control y una fuente DC-DC aislada para la alimentación de los circuitos de disparo, garantizando así un funcionamiento seguro y robusto del sistema.

\subsubsection{Topología de puente trifásico}

La etapa inversora se implementó mediante una topología de puente trifásico de dos niveles como el de la figura \ref{fig:dev_inv_PuenteHTrifasico}, conformada por seis interruptores electrónicos de potencia dispuestos en tres ramas. Cada rama está compuesta por un transistor superior y uno inferior conectados en serie entre los rieles positivo y negativo del bus DC, siendo el punto medio de cada rama la salida correspondiente a una fase del sistema trifásico.

\begin{figure}[H]
\centering
    
    \caption{Esquema de puente H trifásico completo.}
\label{fig:dev_inv_PuenteHTrifasico}
\end{figure}

Esta configuración permite generar tensiones alternas trifásicas equilibradas, desfasadas $120^\circ$ entre sí, y resulta ampliamente utilizada en variadores de frecuencia debido a su simplicidad, robustez y compatibilidad con estrategias de modulación avanzadas como la modulación por vector espacial (SVM). Asimismo, la topología seleccionada ofrece un buen compromiso entre complejidad de implementación, calidad de la forma de onda y pérdidas por conmutación, siendo adecuada para los niveles de potencia considerados en este proyecto.

\subsubsection{Selección de los transistores de potencia}

El puente H trifásico se implementa mediante seis transistores MOSFET de canal N. Esta elección presenta ventajas significativas frente al uso de dispositivos de canal P, principalmente debido a su mayor disponibilidad comercial, menores resistencias de conducción y mejores prestaciones dinámicas. Como contraparte, el control de los transistores del lado alto se vuelve ligeramente más complejo, ya que para su encendido se requiere una tensión superior a $V_{DD}$. Esta limitación se resuelve mediante el uso de circuitos drivers específicos para medio puente.

La potencia requerida en la salida corresponde a la alimentación de un motor trifásico de $1/3 \, HP$, equivalente a $248.56 \, W$. Se asume un factor de potencia de $0.85$, y a partir de la expresión de potencia trifásica se calcula la corriente de línea, obteniéndose un valor eficaz de $0.76 \, A$ y una corriente pico de $1.08 \, A$.

\[
P = \sqrt{3} \, V_L \, I_L \, FP
\]
\[
I_L=\frac{P}{\sqrt{3} \, V_L FP}=\frac{248.56 \, W}{\sqrt{3} \, 220V \, 0.85} = 0.767 \, A
\]
\[
\hat{I_L} \, \sqrt{2} = 1.08 \, A
\]

Considerando una corriente máxima de $1.08 \, A$, una tensión de bus de $320 \, V$ y una frecuencia de conmutación de $2.5 \, kHz$, se seleccionaron los transistores MOSFET \textit{STF24N65M2} de STMicroelectronics. Sus principales características se detallan en la tabla \ref{tab:STF24N65M2_specs}. Este dispositivo se presenta en encapsulado TO-220FP, el cual incorpora aislación eléctrica entre el semiconductor y su carcasa, facilitando el montaje mecánico y reduciendo la complejidad del sistema de aislamiento.

\begin{table}[H]
\centering
\renewcommand{\arraystretch}{1.3} % Aumenta el espaciado para mejor legibilidad
\begin{tabular}{|l|l|}
\hline
\multicolumn{2}{|c|}{\textbf{Características Clave del MOSFET STF24N65M2}} \\
\hline
\textbf{Parámetro} & \textbf{Valor Típico / Máximo} \\
\hline
Tipo de Transistor & N-Channel MDmesh \\
Tensión Máxima Drenaje-Fuente ($V_{DSS}$) & 650 V \\
Corriente Continua Máx. Drenaje ($I_D$ @ 25°C) & 16 A \\
Resistencia Drenaje-Fuente On ($R_{DS(on)}$ máx.) & $230 \, m\Omega$ \\
Disipación de Potencia Máx. ($P_D$ @ 25°C) & $30 \, W$ \\
Carga de Puerta Total ($Q_g$) & $29 \, nC$ \\
Encapsulado & TO-220FP \\
\hline
\end{tabular}
\caption{Especificaciones técnicas principales del MOSFET de potencia STF24N65M2.}
\label{tab:STF24N65M2_specs}
\end{table}

De acuerdo con la curva de área de operación segura de la figura \ref{fig:imgDevSOA-STF24N65M2}, el dispositivo trabaja dentro de condiciones seguras, considerando pulsos de $400 \, \mu s$ y tensión de $320 \, V$ nos da una corriente máxima de operación de $2.5 \, A$, manteniendo un margen de seguridad.

\begin{figure}[H]
\centering
    
    \caption{Área de operación segura del STF24N65M2.}
\label{fig:imgDevSOA-STF24N65M2}
\end{figure}

\subsubsection{Circuito de disparo}

En un inversor trifásico de seis interruptores, una alternativa clásica consiste en emplear tres MOSFETs de canal N y tres de canal P. Sin embargo, esta solución resulta poco conveniente debido a que los dispositivos de canal P presentan valores mayores de resistencia de conducción $R_{DS(on)}$, lo que incrementa las pérdidas y reduce la eficiencia global del sistema. Además, los MOSFETs de canal P con alta tensión de ruptura son menos comunes y considerablemente más costosos.

Por este motivo, se optó por utilizar exclusivamente MOSFETs de canal N. No obstante, esta decisión implica la necesidad de generar una tensión de compuerta superior al potencial del nodo de salida para accionar los transistores superiores del puente. Para resolver este desafío se emplea la técnica de bootstrap mediante el driver de compuerta IR2104, cuyo esquema básico de aplicación se muestra en la figura \ref{fig:img_inv_dev_Esq_IR2104}.

\begin{figure}[H]
\centering
    
    \caption{Esquema básico de implementación del driver IR2104.}
\label{fig:img_inv_dev_Esq_IR2104}
\end{figure}

El IR2104 permite el control de un medio puente cargando un capacitor de bootstrap cuando el transistor inferior se encuentra en conducción. Posteriormente, este capacitor se conecta entre los terminales gate-source del transistor superior, proporcionando la tensión necesaria para su activación. Esta técnica elimina la necesidad de fuentes auxiliares aisladas para los transistores del lado alto, simplificando el diseño y mejorando la eficiencia del sistema.

El integrado dispone de dos entradas de control y tres salidas. El pin SD, cuando se encuentra en nivel lógico HIGH, habilita las salidas, mientras que en nivel LOW las coloca en estado de alta impedancia. El pin IN determina qué transistor conduce: en HIGH se activa el transistor superior y en LOW el inferior. El capacitor de bootstrap se conecta entre los terminales VB y VS. La lógica interna del IR2104 impide la activación simultánea de ambos transistores de un mismo medio puente, evitando situaciones de cortocircuito del bus DC.

Al operar con cargas inductivas, como motores eléctricos, resulta crítico analizar el comportamiento de la corriente durante los eventos de conmutación. Debido a la naturaleza inductiva de la carga, la corriente no puede variar instantáneamente, generándose picos de tensión al intentar interrumpir el flujo de corriente. Para absorber esta energía y proteger los dispositivos de potencia, se requiere una trayectoria de circulación libre de corriente (\textit{freewheeling}). Esta función es cumplida por los diodos intrínsecos de los MOSFETs, conectados en antiparalelo con el canal, los cuales proporcionan un camino seguro para la corriente durante los intervalos de conmutación.

\subsubsection{Aislación galvánica de las señales de control}

Con el objetivo de mantener aislada eléctricamente la etapa de control basada en el microcontrolador de la etapa de potencia del inversor, se implementa una barrera de aislación galvánica mediante el uso de optoacopladores. Dado que las señales de control poseen frecuencias de hasta $2.5 \, kHz$, es necesario emplear dispositivos de alta velocidad.

Los optoacopladores seleccionados son los 6N135, los cuales incorporan un fotodiodo con salida transistorizada de alta velocidad. Este diseño, junto con la conexión separada del fotodiodo, permite mejorar significativamente el tiempo de respuesta respecto a optoacopladores convencionales. La salida es compatible con lógica CMOS, TTL y LSTTL. Para adecuar la polaridad de la señal, se utiliza un transistor complementario que invierte la lógica de salida, tal como se muestra en la figura \ref{fig:img_inv_dev_Esq_6N135}.

\begin{figure}[H]
\centering
    
    \caption{Esquema circuital del circuito de aislación utilizando el optoacoplador 6N135.}
\label{fig:img_inv_dev_Esq_6N135}
\end{figure}

\subsubsection{Simulación}

Con el fin de validar el correcto funcionamiento del driver IR2104, se realizó una simulación de una pierna completa del inversor, utilizando dos MOSFETs y una carga resistiva, alimentada con una tensión de bus de $320 \, V$, como se muestra en la figura \ref{fig:img_inv_dev_Sim_IR2104}.

\begin{figure}[H]
\centering
    
    \caption{Esquemático del circuito simulado para la conmutación de una pierna del inversor.}
\label{fig:img_inv_dev_Sim_IR2104}
\end{figure}

En la figura \ref{fig:img_inv_dev_Sim_Vgs_Id} se presentan las formas de onda de tensión y corriente sobre la carga. Se observa una conmutación limpia y estable, sin picos excesivos ni comportamientos anómalos, lo que confirma la correcta operación del circuito de disparo y su adecuada adaptación para su implementación en el inversor trifásico desarrollado.

\begin{figure}[H]
\centering
    
    \caption{Simulación de tensión sobre la carga en trazo verde y corriente a través de la carga en trazo azul.}
\label{fig:img_inv_dev_Sim_Vgs_Id}
\end{figure}

\subsubsection{Diseño de circuito impreso}

El diseño del PCB del inversor se realizó con una topología simple y funcional, como se muestra en las figuras \ref{fig:img_inv_dev_PCB_Front} y \ref{fig:img_inv_dev_PCB_Back}. Los seis transistores del puente H trifásico se disponen en las proximidades de los conectores del bus de continua y de la salida hacia el motor, con el objetivo de minimizar la longitud de las pistas de potencia y reducir las inductancias parásitas.

Las pistas correspondientes a la etapa de potencia se dejaron sin recubrimiento de máscara antisoldante, permitiendo su estañado. Esta práctica incrementa la sección transversal efectiva del conductor, disminuyendo la resistencia eléctrica y, en consecuencia, las pérdidas por conducción.

Los circuitos de disparo se ubican en la zona central de la placa y se implementan bajo una estructura modular en forma de celda, la cual se replica tres veces. Cada celda incluye su respectivo integrado IR2104 y los optoacopladores asociados a ambas señales de control del medio puente, facilitando el ruteo, la repetitividad del diseño y la escalabilidad del sistema.

En la parte inferior de la placa se localizan los conectores correspondientes a las señales de modulación provenientes del sistema de control, así como la entrada de alimentación de $12 \, V$ provista por el convertidor DC-DC auxiliar.
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

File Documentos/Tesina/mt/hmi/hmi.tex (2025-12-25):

\label{sec:2_mt_hmi}

\subsection{HMI}

La principal función de este módulo es poder darle al usuario una interfaz de configuración y control del comportamiento del sistema. Habitualmente son dispositivos que leen y controlan las variables del sistema y se las presenta al usuario en un formato amigable, abstrayéndolo de variables eléctricas y transformando la información colectada en su representación final y más adecuada para la aplicación para la cual se la diseño. Además, interactúa con dispositivos eléctricos y electrónicos a través de puertos de comunicación,
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

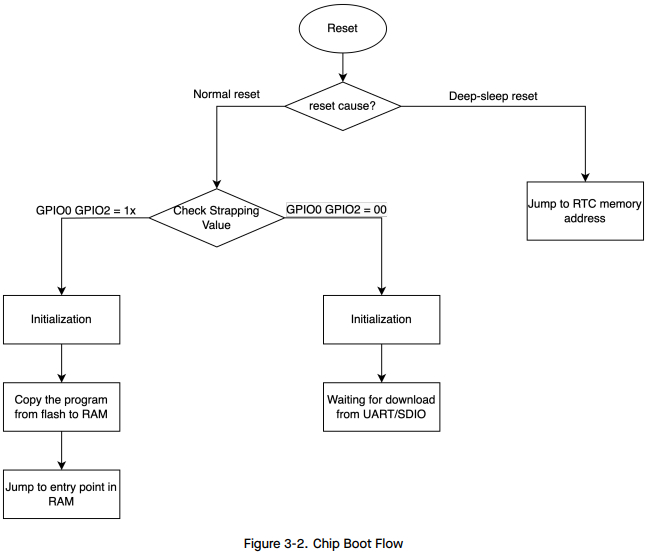
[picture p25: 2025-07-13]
Hardware/PCB_MicroHMI/img/Boot_ESP.png

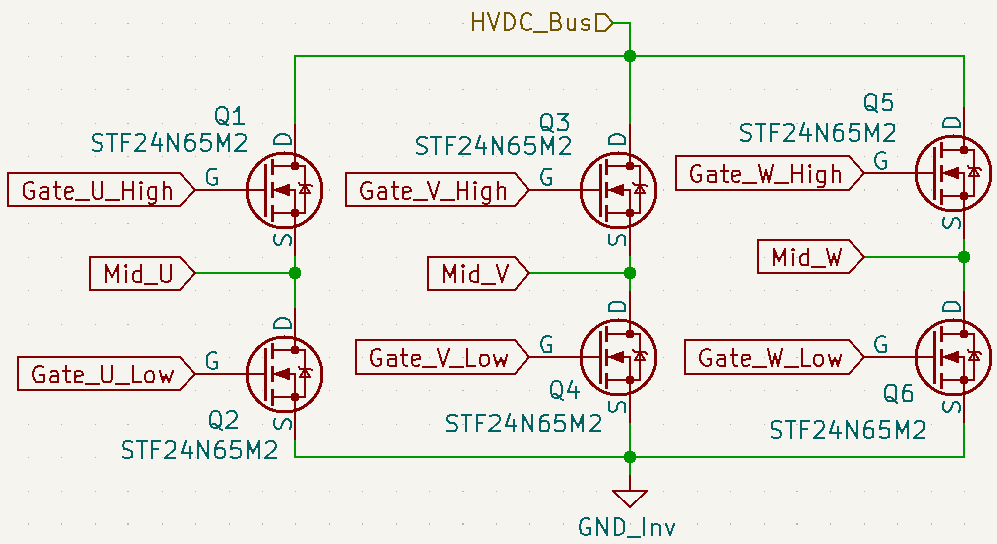
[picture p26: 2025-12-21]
Documentos/Poster/img/PuenteH_Inversor.png

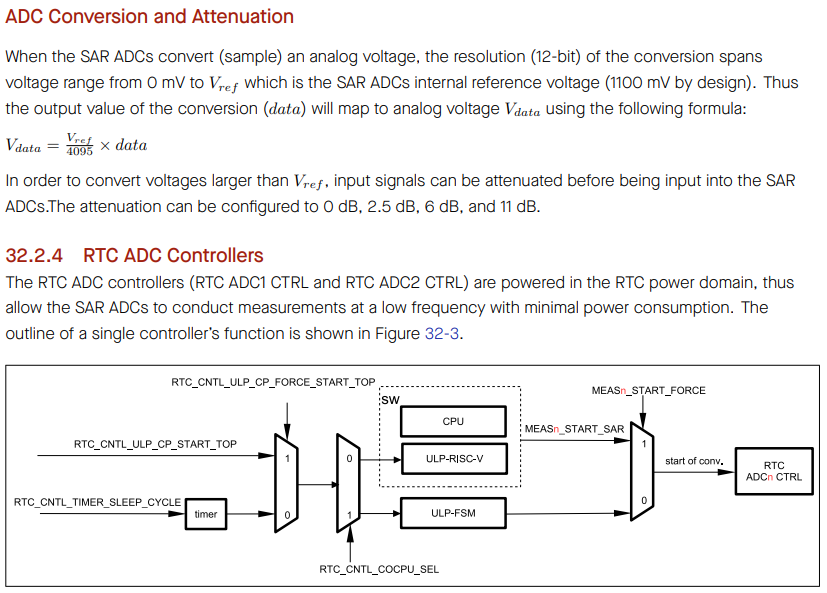
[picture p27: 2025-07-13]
Hardware/PCB_MicroHMI/img/ADC.png

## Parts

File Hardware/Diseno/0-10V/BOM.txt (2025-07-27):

Ref.	Mfg.		Part No.	Description
---------------- Salida 0-10V aislada -------------------
C1		--			--			capacitor, 100µF
C2		--			--			capacitor, 100µF
M1		Fairchild	2N7002		MOSFET
Q2		NXP	BC547C	bipolar 	transistor
R1		--			--			resistor, 10K
R2		--			--			resistor, 28
R3		--			--			resistor, 59K
R4		--			--			resistor, 102
R5		--			--			resistor, 1K
U1		(unknown)	4N25		(unknown 3rd party model)
------------------ Entradas aisladas ---------------------
R1		--	--		resistor,	1K
R5		--	--		resistor,	390
U1		(unknown)	4N25		(unknown 3rd party model)

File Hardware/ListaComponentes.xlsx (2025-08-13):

Tipo | Componente | Paquete / Caracteristica | Denominacion EasyEDA | Marca | Precio LCSC | Q | Precio minimo | Q Necesaria | Placa | Uso | Comentarios | Denominacion Mouser | Marca2 | Precio Mouser | Q3
Bornera | Terminal barrier | Three terminals | DBT50G-9.5-3P-BK-P OGC (https://lcsc.com/product-detail/Barrier-Terminal-Blocks_DORABO-DBT50G-9-5-3P-BK-P-OGC_C395959.html) | dorabo | 0.3712 | 5 | 1.856
Bornera | Terminal block | Bornera 2p | WJ500V-5.08-2P (https://lcsc.com/product-detail/Screw-Terminal-Blocks_Ningbo-Kangnex-Elec-WJ500V-5-08-2P_C8465.html) | Ningbo | 0.0991 | 5 | 0.495
Bornera | Terminal block | Bornera 3p | WJ500V-5.08-3P (https://lcsc.com/product-detail/Screw-Terminal-Blocks_Ningbo-Kangnex-Elec-WJ500V-5-08-3P_C72334.html) | Ningbo | 0.1707 | 5 | 0.853 |  |  | Excluida
Boton |  |  | TS-1187A-B-A-B (https://lcsc.com/product-detail/Tactile-Switches_XKB-Connection-TS-1187A-B-A-B_C318884.html) | XKB | 0.019 | 20 | 0.380 |  |  |  |  | EVQ-PLWA15 (https://ar.mouser.com/ProductDetail/Panasonic/EVQ-PLWA15?qs=WwqriLBepZsSfxlxZfFnlQ%3D%3D) | Panasonic (https://ar.mouser.com/manufacturer/panasonicec/) | 0.41 | 1
Boton |  |  |  |  |  |  | 0.000 |  |  |  |  | STM32F103C8T6 (https://ar.mouser.com/ProductDetail/STMicroelectronics/STM32F103C8T6?qs=bhCVus9SdFtq6kqxsU5%2FDA%3D%3D) | STM | 5.54 | 1
Buzzer |  | 2.3Khz | TMB12A03 (https://lcsc.com/product-detail/Buzzers_Jiangsu-Huaneng-Elec-TMB12A03_C96222.html) | Jiangsu | 0.1908 | 5 | 0.954
Cable + Terminal |  |  | 2.54-2P DT 200mm 24AWG (https://lcsc.com/product-detail/Dupont-wire-terminal-block-wire-electronic-wire_SHOU-HAN-2-54-2P-DT-200mm-24AWG_C5363463.html) | SHOU HAN | 0.068 | 10 | 0.680
Cable + Terminal |  |  | 2.54-2P DT 200mm 24AWG (https://lcsc.com/product-detail/Dupont-wire-terminal-block-wire-electronic-wire_SHOU-HAN-2-54-2P-DT-200mm-24AWG_C5363463.html) |  |  |  | 0.000
Cable + Terminal |  |  | 2.54-6P DT 200mm 24AWG (https://lcsc.com/product-detail/Dupont-wire-terminal-block-wire-electronic-wire_SHOU-HAN-2-54-6P-DT-200mm-24AWG_C5363467.html) |  |  |  | 0.000
Cable + Terminal |  |  | 2.54-4P DT 200mm 24AWG (https://lcsc.com/product-detail/Dupont-wire-terminal-block-wire-electronic-wire_SHOU-HAN-2-54-4P-DT-200mm-24AWG_C5363465.html) |  |  |  | 0.000
Cable + Terminal |  |  | 2.54-5P DT 200mm 24AWG (https://lcsc.com/product-detail/Dupont-wire-terminal-block-wire-electronic-wire_SHOU-HAN-2-54-5P-DT-200mm-24AWG_C5363466.html) |  |  |  | 0.000
Capacitor |  | 100nF | CC0603KRX7R9BB104 (https://lcsc.com/product-detail/Multilayer-Ceramic-Capacitors-MLCC-SMD-SMT_YAGEO-CC0603KRX7R9BB104_C14663.html) | yageo | 0.0024 | 100 | 0.240
Capacitor |  | 10nF | CC0603KRX7R9BB103 (https://lcsc.com/product-detail/Multilayer-Ceramic-Capacitors-MLCC-SMD-SMT_YAGEO-CC0603KRX7R9BB103_C100042.html) | yageo | 0.0022 | 100 | 0.220
Capacitor |  | 22pF | CC0603FRNPO9BN220 (https://lcsc.com/product-detail/Multilayer-Ceramic-Capacitors-MLCC-SMD-SMT_YAGEO-CC0603FRNPO9BN220_C326840.html) | yageo | 0.0086 | 50 | 0.430
Capacitor |  | 20pF | CC0603FRNPO9BN200 (https://lcsc.com/product-detail/Multilayer-Ceramic-Capacitors-MLCC-SMD-SMT_YAGEO-CC0603FRNPO9BN200_C326779.html) | yageo | 0.0087 | 50 | 0.435
Capacitor |  | 12pF | CC0603FRNPO9BN120 (https://lcsc.com/product-detail/Multilayer-Ceramic-Capacitors-MLCC-SMD-SMT_YAGEO-CC0603FRNPO9BN120_C519482.html) | yageo | 0.0086 | 50 | 0.430 |  |  |  |  |  |  |  |  | Faltan las de la placa del micro
Capacitor | electrolitico | 10u | RVT1V100M0405 (https://www.lcsc.com/product-detail/Aluminum-Electrolytic-Capacitors---SMD_ROQANG-RVT1V100M0405_C72485.html) | roqanc | 0.0212 | 20 | 0.424
Capacitor | electrolitico | 22u | RVT1C220M0405 (https://lcsc.com/product-detail/Aluminum-Electrolytic-Capacitors-SMD_ROQANG-RVT1C220M0405_C72502.html) | roqanc | 0.0204 | 20 | 0.408
Capacitor | electrolitico | 4700uF - 25V | KM478M025K25RR0VH2FP0 (https://lcsc.com/product-detail/Aluminum-Electrolytic-Capacitors-Leaded_CX-Dongguan-Chengxing-Elec-KM478M025K25RR0VH2FP0_C45070.html) | cx | 0.3452 | 5 | 1.726 | 2
Capacitor |  | 100uF - 400V | NCC EKMQ401VSN101MP25S (https://lcsc.com/product-detail/Horn-Type-Electrolytic-Capacitors_NCC-EKMQ401VSN101MP25S_C1586377.html) | ncc | 1.6017 | 2 | 3.203 | 1
Capacitor |  | 220uF - 400V | CapXon HP221M400N310A (https://lcsc.com/product-detail/Horn-Type-Electrolytic-Capacitors_CapXon-HP221M400N310A_C531139.html) | CapXon (https://lcsc.com/brand-detail/810.html) | 1.9144 | 1 | 1.914 |  |  | Excluido
Conector | XT90 | XT90 | XT90PW-M.G.Y (https://lcsc.com/product-detail/plug_Changzhou-Amass-Elec-XT90PW-M-G-Y_C3040689.html) |  | 0.8396 | 2 | 1.679
Conector | Wire-Board | 2P 5.08mm | CH5.08-2A (https://lcsc.com/product-detail/Wire-To-Board-Connector_BOOMELE-Boom-Precision-Elec-CH5-08-2A_C27692.html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) | Boomele | 0.0334 | 20 | 0.668 | 2 | Conv-Inv
Conector |  | Female | CH5.08-2Y (https://lcsc.com/product-detail/Housings-Wire-To-Board-Wire-To-Wire_BOOMELE-Boom-Precision-Elec-CH5-08-2Y_C5128300.html) | Boomele | 0.0229 | 20 | 0.458 | 2
Conector |  | 3P 5.08mm | CH5.08-3A (https://lcsc.com/product-detail/Wire-To-Board-Connector_BOOMELE-Boom-Precision-Elec-CH5-08-3A_C23514.html) | Boomele | 0.05 | 10 | 0.500 | 2 | Inv-Intefaz
Conector |  | Female | CH5.08-3Y (https://lcsc.com/product-detail/Housings-Wire-To-Board-Wire-To-Wire_BOOMELE-Boom-Precision-Elec-CH5-08-3Y_C45331.html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) | Boomele | 0.0373 | 20 | 0.746 | 2
Conector |  | Male 4P 2.54mm | ZX-XH2.54-4PZZ (https://lcsc.com/product-detail/Wire-To-Board-Connector_Megastar-ZX-XH2-54-4PZZ_C7429634.html) | Megastar | 0.0092 | 20 | 0.184 | 4 | Micro-Inv
Conector |  | Female | ZX-XH2.54-4PJK (https://lcsc.com/product-detail/Housings-Wire-To-Board-Wire-To-Wire_Megastar-ZX-XH2-54-4PJK_C7462724.html) | Megastar | 0.0062 | 50 | 0.310 | 4
Conector |  | Male 2P 2.54mm | ZX-XH2.54-2PZZ (https://lcsc.com/eda_search?q=C7429632&&type=1) | Megastar | 0.0054 | 50 | 0.270 | 8 | Inter-Conv, Inter-Inv, Inter-Micro, Inter-Cooler
Conector |  | Female | ZX-XH2.54-2PJK (https://lcsc.com/product-detail/Housings-Wire-To-Board-Wire-To-Wire_Megastar-ZX-XH2-54-2PJK_C7462722.html) | Megastar | 0.004 | 100 | 0.400 | 8
Conector |  | Male 5P 2.54mm | ZX-HA2.54-5PZZ (https://lcsc.com/product-detail/Wire-To-Board-Connector_Megastar-ZX-HA2-54-5PZZ_C7429617.html) | Megastar | 0.0274 | 10 | 0.274 | 2 | Cnv-Micro
Conector |  | Female | ZX-XH2.54-5PJK (https://lcsc.com/product-detail/Housings-Wire-To-Board-Wire-To-Wire_Megastar-ZX-XH2-54-5PJK_C7462725.html) | Megastar | 0.0081 | 50 | 0.405 | 2
Conector | IDC | Header 2x5P | 2.54-2*5P (https://lcsc.com/product-detail/IDC-Connectors_BOOMELE-Boom-Precision-Elec-2-54-2-5P_C5665.html) | Boomele | 0.0744 | 10 | 0.744 | 3 | Micro-Programador, HMI-Program
Conector |  | Three Piece 2x5P | 2.54-2*5P (https://lcsc.com/product-detail/IDC-Connectors_BOOMELE-Boom-Precision-Elec-2-54-2-5P_C8373.html) | Boomele | 0.0891 | 10 | 0.891 | 4
Diodo |  | Mur860ct | MUR860CT (https://lcsc.com/product-detail/Fast-Recovery-High-Efficiency-Diodes_Yangzhou-Yangjie-Elec-Tech-MUR860CT_C700469.html) | Yangzhou (https://lcsc.com/brand-detail/11514.html) | 0.3461 | 2 | 0.692 |  | Conversor |  |  | MURH860CTG (https://ar.mouser.com/ProductDetail/onsemi/MURH860CTG?qs=Gev%252BmEvV0iZw86OhP5%2F%2FEw%3D%3D) | onsemi (https://ar.mouser.com/manufacturer/onsemi/) | 1.11 | 2
Diodo |  | Mur860 | MUR860 (https://lcsc.com/product-detail/Fast-Recovery-High-Efficiency-Diodes_RUILON-Shenzhen-Ruilongyuan-Elec-MUR860_C2944306.html) | Ruilon | 0.3797 | 5 | 1.898 |  | Conversor |  |  | MUR880EG (https://ar.mouser.com/ProductDetail/onsemi/MUR880EG?qs=Gev%252BmEvV0iZuzgGNI9B7nA%3D%3D) | onsemi (https://ar.mouser.com/manufacturer/onsemi/) | 0.7 | 5 | ACA faltan los pines y los cables
Diodo |  |  | 1N5819WS S4 (https://lcsc.com/product-detail/Schottky-Diodes_JSMSEMI-1N5819WS-S4_C2927280.html) | jsmsemi | 0.0092 | 5 | 0.046 |  | Micro | Excluido
Diodo |  | mur260 | MUR260S (https://lcsc.com/product-detail/Fast-Recovery-High-Efficiency-Diodes_amsem-MUR260S_C18336929.html) | amsem | 0.00418 | 5 | 0.021 |  | Inversor | Complemento IR2104
Diodo | Zener | bzv55c3v3 | BZV55C3V3 (https://lcsc.com/product-detail/Zener-Diodes_LGE-BZV55C3V3_C545323.html) | LGE | 0.0153 | 10 | 0.153 | 1 | Conversor |  |  | BZV55C3V3 L0G (https://ar.mouser.com/ProductDetail/Taiwan-Semiconductor/BZV55C3V3-L0G?qs=KwaGCOX4wIbLKgQCCPXAFw%3D%3D) | Taiwan | 0.23 | 2
Diodo | ESD | Supresor trans. | BSD5C031V (https://lcsc.com/product-detail/ESD-and-Surge-Protection-TVS-ESD_BORN-BSD5C031V_C151984.html) | Born | 0.0284 | 20 | 0.568 |  | Micro
Fuente aislada |  | b1205s-2wr2 | B1205S-2WR2 (https://lcsc.com/product-detail/Isolated-Power-Modules_YLPTEC-B1205S-2WR2_C2992386.html) | YLPTEC | 1.4356 | 3 | 4.307 | 2 | Micro |  |  | 1779405241 (https://ar.mouser.com/ProductDetail/Wurth-Elektronik/1779405241?qs=amGC7iS6iy9JBIrkcvaziA%3D%3D) | Wurth Elektronik (https://ar.mouser.com/manufacturer/wurth-elektronik/) | 4.35 | 3 | Faltan los housing terminals
Fuente aislada |  | b1212s-2wr3 | B1212S-2WR3 (https://lcsc.com/product-detail/Isolated-Power-Modules_DEXU-Electronics-B1212S-2WR3_C3019582.html) | DEXU | 1.2629 | 2 | 2.526 | 1 | Inversor |  |  | TBA 2-1212 (https://ar.mouser.com/ProductDetail/TRACO-Power/TBA-2-1212?qs=byeeYqUIh0ON8U3yVOJqLg%3D%3D) | TRACO Power (https://ar.mouser.com/manufacturer/traco-power/) | 4.22 | 2
Fusible |  | 40Amp | 0287040.PXCN (https://lcsc.com/product-detail/Automotive-Fuses_Littelfuse-0287040-PXCN_C142687.html) |  | 0.1021 | 5 | 0.510 |  | Conversor
Insertos |  | Insertos roscados | m4*8*6 (https://lcsc.com/product-detail/Through-hole-embedded-round-nuts_ZHONGYI-m4-8-6_C20618342.html) | zhongyi | 0.048 | 20 | 0.960
Integrados | Zener program | TL431 | TL431 (https://lcsc.com/product-detail/Voltage-Reference_Guangdong-Hottech-TL431_C181104.html) | GuangDong | 0.0347 | 20 | 0.694 | 1 | Conversor
Integrados | Controlador | TL494 | JSMSEMI TL494 (https://lcsc.com/product-detail/DC-DC-Converters_JSMSEMI-TL494_C5356108.html) | JSMSEMI | 0.0922 | 5 | 0.461 | 1 | Conversor
Integrados | Mos driver | ir2104 | IR2104STRPBF-JSM (https://lcsc.com/product-detail/Gate-Drivers_JSMSEMI-IR2104STRPBF-JSM_C5804631.html) | jsmsemi | 0.4407 | 4 | 1.763 | 3 | Inversor
LDO |  | ams1117 | AMS1117-3.3 (https://lcsc.com/product-detail/Voltage-Regulators-Linear-Low-Drop-Out-LDO-Regulators_UMW-Youtai-Semiconductor-Co-Ltd-AMS1117-3-3_C347222.html) | UMW | 0.04 | 5 | 0.200 | 2 | Micro |  |  | TLV1117LV33DCYR (https://ar.mouser.com/ProductDetail/Texas-Instruments/TLV1117LV33DCYR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) | Texas Instruments (https://ar.mouser.com/manufacturer/texas-instruments/) | 0.22 | 2
Led | Led Green | 603 x 1.6x0.8mm | XL-1608UGC-04 (https://lcsc.com/product-detail/LED-Indication-Discrete_XINGLIGHT-XL-1608UGC-04_C965804.html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) |  | 0.0044 | 100 | 0.440 |  | Conversor, inversor, micro |  |  | APT1608CGCK (https://ar.mouser.com/ProductDetail/Kingbright/APT1608CGCK) |  | 0.24 | 3
Led | Led Red | 604 x 1.6x0.8mm | XL-1608SURC-06 (https://lcsc.com/product-detail/LED-Indication-Discrete_XINGLIGHT-XL-1608SURC-06_C965799.html) |  | 0.0032 | 100 | 0.320 |  | Micro |  |  | APT1608SURC (https://ar.mouser.com/ProductDetail/Kingbright/APT1608SURC?qs=sGAEpiMZZMv0DJfhVcWlK8AiAHwfAGPKjtEXvGpM2Z8%3D) |  | 0.41 | 3
Led | Led Yellow | 605 x 1.6x0.8mm | XL-1608UYC-06 (https://lcsc.com/product-detail/LED-Indication-Discrete_XINGLIGHT-XL-1608UYC-06_C965802.html) |  | 0.0059 | 100 | 0.590 |  | Micro |  |  | APT1608SYC (https://ar.mouser.com/ProductDetail/Kingbright/APT1608SYC?qs=sGAEpiMZZMv0DJfhVcWlK8AiAHwfAGPKwrpprqvgb5g%3D) |  | 0.17 | 3
Led | Rectangular verde | Green 2x5x7mm Square | XL-257SYGD-L (https://lcsc.com/product-detail/LED-Indication-Discrete_XINGLIGHT-XL-257SYGD-L_C5440572.html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) |  | 0.0294 | 20 | 0.588 |  | Inter
Microcontrolador |  | STM32 | STM32F103C8T6 (https://lcsc.com/product-detail/Microcontrollers-MCU-MPU-SOC_STMicroelectronics-STM32F103C8T6_C8734.html) | STM | 1.0868 | 1 | 1.087 |  | Micro
Microcontrolador |  | ESP32 | ESP32-WROOM-32E-N16 (https://lcsc.com/product-detail/WiFi-Modules_Espressif-Systems-ESP32-WROOM-32E-N16_C701343.html) | espressif | 4.8817 | 1 | 4.882 |  | Micro
Opto |  | pc817 | PC817C (https://lcsc.com/product-detail/Transistor-Photovoltaic-Output-Optoisolators_UMW-Youtai-Semiconductor-Co-Ltd-PC817C_C3008368.html) | Wuxi | 0.0348 | 20 | 0.696 | 2 | Conversor |  |  | PC817X1NSZ1B (https://ar.mouser.com/ProductDetail/Sharp-Microelectronics/PC817X1NSZ1B?qs=rrS6PyfT74e4O%2FoD5P1nvg%3D%3D) | Sharp | 0.67 | 5
Opto |  | 6n135 | 6N135M (https://lcsc.com/product-detail/Transistor-Photovoltaic-Output-Optoisolators_onsemi-6N135M_C194136.html) | onsemi | 0.7071 | 10 | 7.071 | Remplazado
Opto |  | 6n135s | 6N135S (https://lcsc.com/product-detail/Logic-Output-Optoisolators_Slkor-SLKORMICRO-Elec-6N135S_C2918949.html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) | Slkor (https://lcsc.com/brand-detail/11608.html?s_z=n_6n135) | 0.352 | 10 | 3.520 | 6 | Inversor
Oscilador |  | Osc 8Mhz | X49SM8MSD2SC (https://lcsc.com/product-detail/Crystals_YXC-Crystal-Oscillators-X49SM8MSD2SC_C12674.html) | YXC | 0.0873 | 5 | 0.436
Oscilador |  | Osc 32.768Khz | Oscilador 32.768Khz (https://lcsc.com/product-detail/Crystals_Seiko-Epson-Q13FC13500004_C32346.html) | Seiko | 0.1924 | 5 | 0.962
Porta Fusible |  | Blade fuse holder | XF-509P (https://lcsc.com/product-detail/Fuseholders_XFCN-XF-509P_C41371872.html) |  | 0.244 | 5 | 1.220 |  | Conversor
Potenciometro |  | 5K - smd | VGF39NCHXT-B502 (https://lcsc.com/product-detail/Potentiometers-Variable-Resistors_HDK-Hokuriku-Elec-Industry-VGF39NCHXT-B502_C22461636.html) | HDK | 0.0796 | 5 | 0.398
Resistor |  | 10k | RC0603FR-0710KL (https://lcsc.com/product-detail/Chip-Resistor-Surface-Mount_YAGEO-RC0603FR-0710KL_C98220.html) | yageo | 0.0011 | 100 | 0.110
Resistor |  | 1k | RC0603FR-071KL (https://lcsc.com/product-detail/Chip-Resistor-Surface-Mount_YAGEO-RC0603FR-071KL_C22548.html) | yageo | 0.001 | 100 | 0.100
Resistor | 603 | 0ohm | RC0603JR-070RL (https://lcsc.com/product-detail/Chip-Resistor-Surface-Mount_YAGEO-RC0603JR-070RL_C95177.html) | yageo | 0.0011 | 100 | 0.110
Resistor | 805 | 0ohm | RC0805JR-070RL (https://lcsc.com/product-detail/Chip-Resistor-Surface-Mount_YAGEO-RC0805JR-070RL_C96345.html) | yageo | 0.0019 | 100 | 0.190
Resistor | 1205 | 0ohm | RC1206FR-070RL (https://lcsc.com/product-detail/Chip-Resistor-Surface-Mount_YAGEO-RC1206FR-070RL_C137394.html) | yageo | 0.0036 | 100 | 0.360
Resistor | 603 | 1.2k | RC0603FR-071K2L (https://lcsc.com/product-detail/Chip-Resistor-Surface-Mount_YAGEO-RC0603FR-071K2L_C114605.html) | yageo | 0.0012 | 100 | 0.120
Resistor | 603 | 10 Ohm | RC0603FR-0710RL (https://lcsc.com/product-detail/Chip-Resistor-Surface-Mount_YAGEO-RC0603FR-0710RL_C109318.html) | yageo | 0.0027 | 100 | 0.270
Resistor | 603 | 680 Ohm | RC0603FR-07680RL (https://lcsc.com/product-detail/Chip-Resistor-Surface-Mount_YAGEO-RC0603FR-07680RL_C112310.html?s_z=s_YAGEO) | yageo | 0.0012 | 100 | 0.120 |  |  |  |  | Lo necesito??
Resistor | 603 | 4.7K | RC0603FR-074K7L (https://lcsc.com/product-detail/Chip-Resistor-Surface-Mount_YAGEO-RC0603FR-074K7L_C99782.html?s_z=s_YAGEO) | yageo | 0.0011 | 100 | 0.110 |  |  |  |  | Lo necesito??
Resistor | 603 | 1.2k | RC0603FR-071K2L (https://www.lcsc.com/product-detail/Chip-Resistor---Surface-Mount_YAGEO-RC0603FR-071K2L_C114605.html) | yageo | 0.0012 | 100 | 0.120
Resistor | 603 | 3.9k | RC0603FR-073K9L (https://www.lcsc.com/product-detail/Chip-Resistor---Surface-Mount_YAGEO-RC0603FR-073K9L_C114616.html) | yageo | 0.0012 | 100 | 0.120
Ring Terminal | RNB5.5-6 | 6.5mm internal | JIDC RNB5.5-6-90D (https://lcsc.com/product-detail/image/RNB5-5-6-90D_C42428764.html) | jidc | 0.1116 | 5 | 0.558 |  |  | Cable - Bornes de entrada
Ring Terminal |  | 4.3mm internal | RNB5.5-4S (https://lcsc.com/product-detail/Ring-Terminal_JIDC-RNB5-5-4S_C42428758.html) | jidc | 0.0721 | 10 | 0.721 |  |  | Conexión fuente 12V - Cable y para Borne entrada - PCB
Sensor Hall |  | acs712 | ACS712ELCTR-05B-T (https://lcsc.com/product-detail/Current-Sensors_Allegro-MicroSystems-LLC-ACS712ELCTR-05B-T_C44471.html) | Allegro | 1.1452 | 1 | 1.145 | 1 | Conversor |  |  | ACS712ELCTR-05B-T (https://ar.mouser.com/ProductDetail/Allegro-MicroSystems/ACS712ELCTR-05B-T?qs=pUKx8fyJudDs65Rkshv5ug%3D%3D) | Allegro | 2.89 | 1
TestPoint |  |  | RH-5000 (https://lcsc.com/product-detail/Test-Points-Test-Rings_ronghe-RH-5000_C5277086.html) | ronghe | 0.074 | 20 | 1.480
Transistor | Trans PNP | ss8550 | SS8550S (https://lcsc.com/product-detail/Bipolar-BJT_FOSAN-SS8050S_C22395784.html) |  | 0.0094 | 50 | 0.470 |  | Conversor |  |  | MMSS8050-L-TP (https://ar.mouser.com/ProductDetail/Micro-Commercial-Components-MCC/MMSS8050-L-TP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) |  | 0.083 | 10
Transistor | Trans NPN | ss8050 | SS8050S (https://lcsc.com/product-detail/Bipolar-BJT_FOSAN-SS8050S_C22395784.html) |  | 0.0094 | 50 | 0.470 |  | Inversor y conversor |  |  | MMSS8550-H-TP (https://ar.mouser.com/ProductDetail/Micro-Commercial-Components-MCC/MMSS8550-H-TP) |  | 0.135 | 10
Transistor | IRFP4110 | TO220 | IRFB4110(UMW) (https://lcsc.com/product-detail/MOSFETs_UMW-Youtai-Semiconductor-Co-Ltd-IRFB4110-UMW_C18209200.html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) | UMW | 0.5867 | 10 | 5.867 |  | Conversor |  |  | IRFB4110PBF (https://ar.mouser.com/ProductDetail/Infineon-Technologies/IRFB4110PBF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) |  | 2.31 | 10
Transistor | tk8a65 | TO220 | TK8A65D (https://lcsc.com/product-detail/MOSFETs_TOSHIBA-TK8A65D-STA4-Q-M-_C2990817.html) | Toshiba | 0.5286 | 10 | 5.286 |  | Inversor

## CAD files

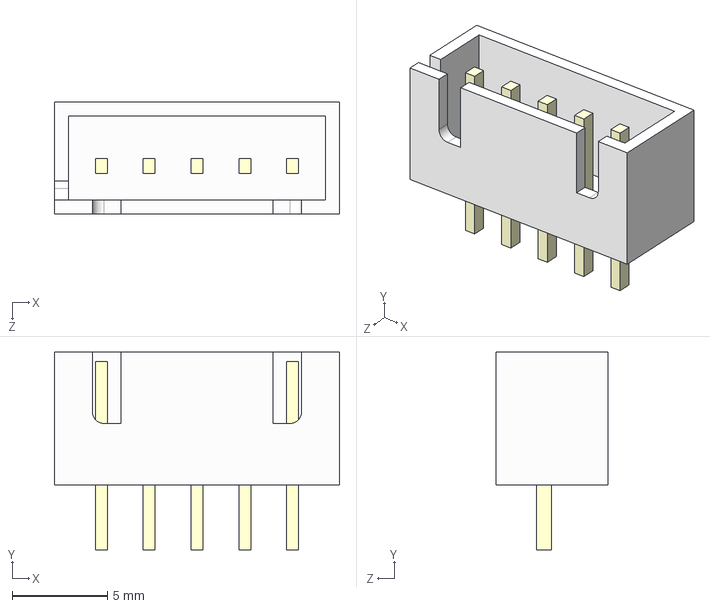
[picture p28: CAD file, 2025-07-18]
Hardware/PCB_Conversor/Modelos/Conectores/Conector P2.54mm 5P Male.step
15.0 x 10.4 x 5.90 mm

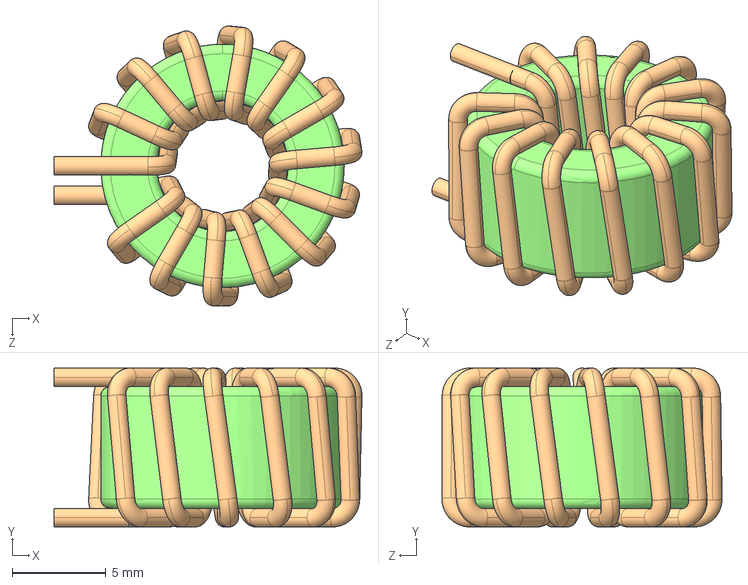
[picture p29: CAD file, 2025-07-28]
Hardware/PCB_Conversor/Modelos/Inductor/Toroide - P7.68mm.step
16.4 x 8.49 x 15.0 mm

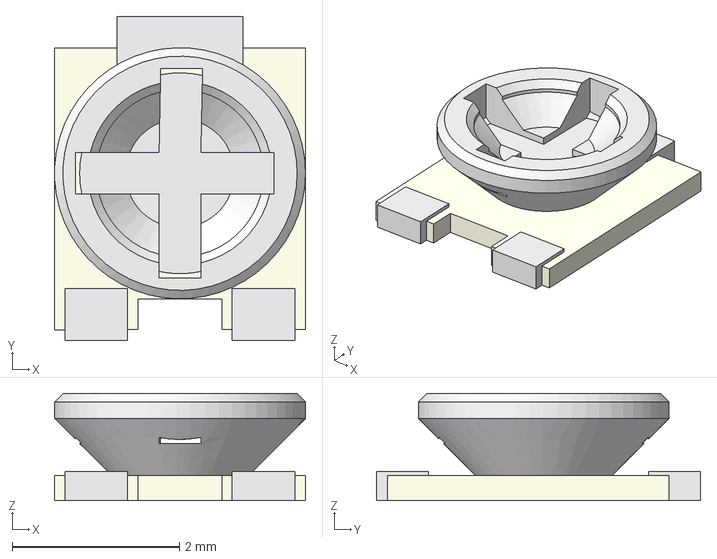
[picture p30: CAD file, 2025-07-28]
Hardware/PCB_Conversor/Modelos/Potenciometro/3303W-3.step
3.00 x 3.88 x 1.28 mm

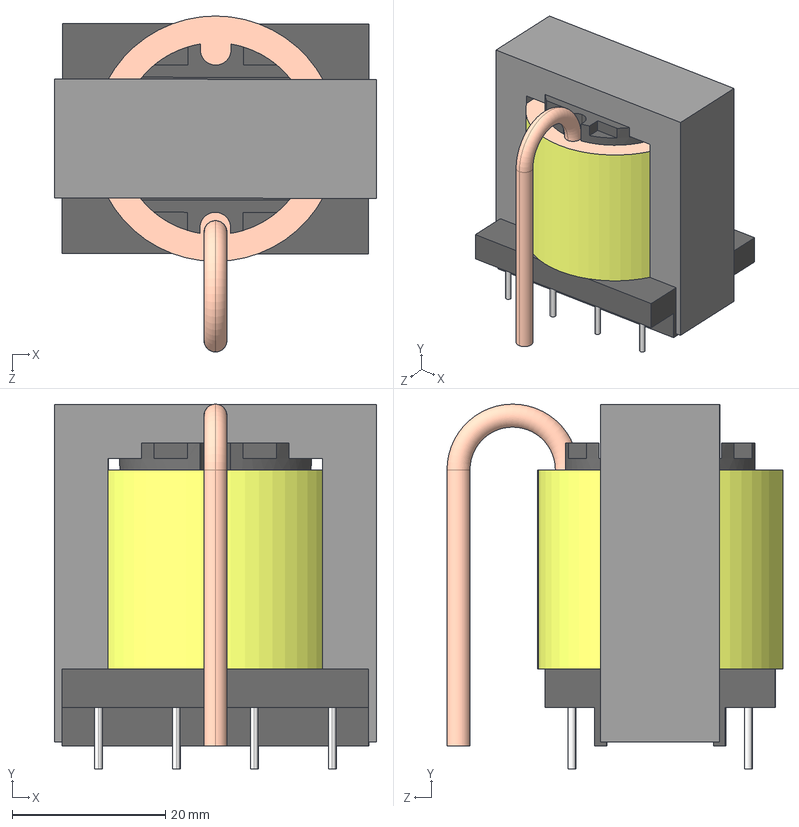
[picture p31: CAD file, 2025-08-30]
Hardware/PCB_Conversor/Modelos/Transformador/EDT42.step
42.0 x 47.6 x 43.8 mm
Bobinado
Carrete
Nucleo

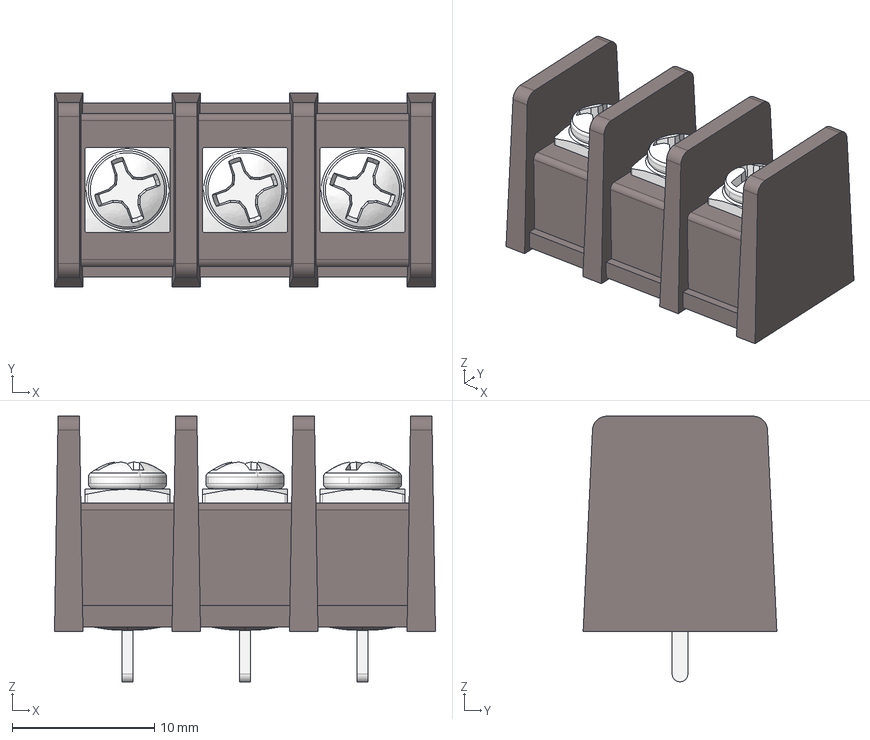
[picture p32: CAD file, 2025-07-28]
Hardware/PCB_Integradora/Modelos/Conectores/DG35C-B-03P-1Y-00L (H).step
26.8 x 13.6 x 18.6 mm

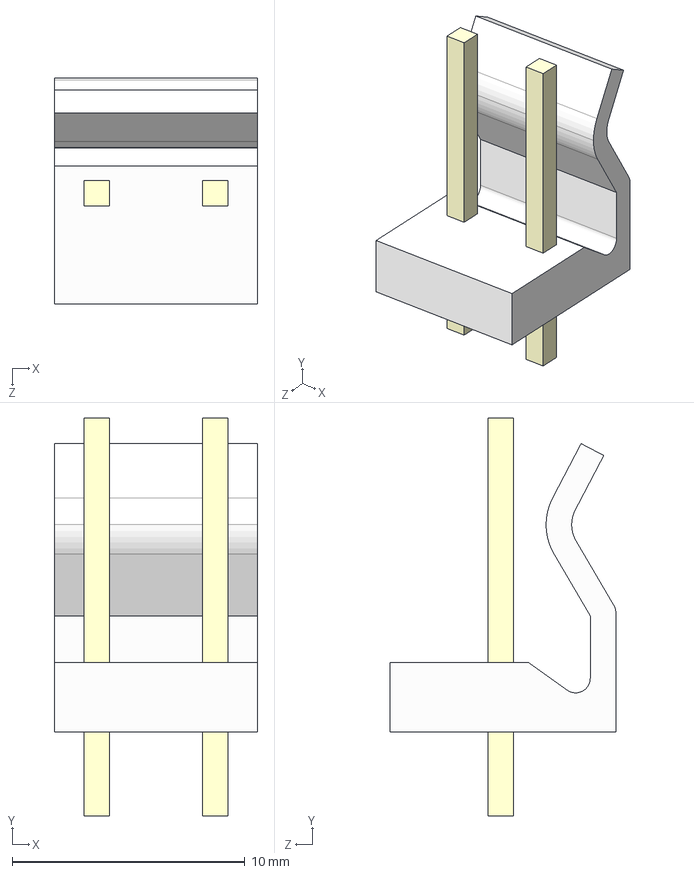
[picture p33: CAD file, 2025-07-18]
Hardware/PCB_Inversor/Modelos/Conectores/Conector P5.08mm 2P Male.step
8.74 x 17.1 x 9.70 mm

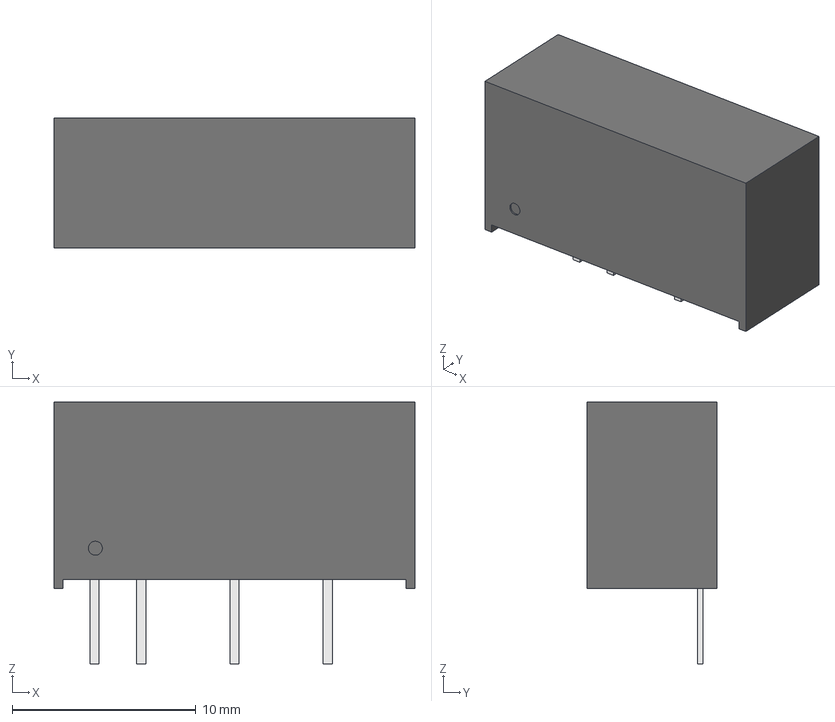
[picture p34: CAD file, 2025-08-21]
Hardware/PCB_Inversor/Modelos/FuenteAlimentacion/MORNSUN_BxxxxS-2WR2.step
19.6 x 7.05 x 14.3 mm

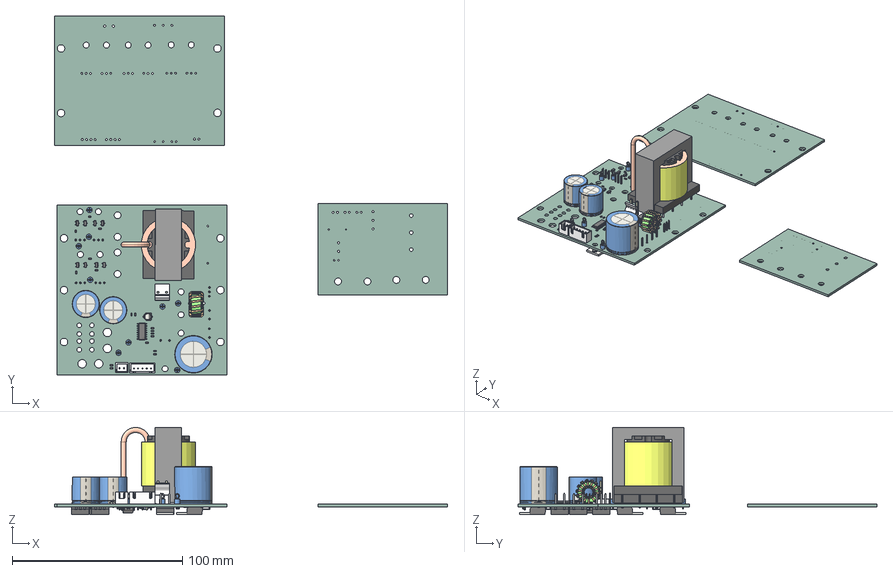
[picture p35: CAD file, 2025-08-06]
Hardware/PCB_Inversor/PCB_Inversor.step
231.3 x 211.2 x 51.2 mm
R_0603_1608Metric x 28
Conector P2.54mm 5P Male
CP_Elec_4x5.4
TestPoint_Loop_D2.60mm_Drill1.6mm_Beaded x 9
CP_Radial_D16.0mm_P7.50mm x 2
CP_Radial_D22.0mm_P10.00mm_SnapIn
SOT-23 x 8
LED_0603_1608Metric
Conector P5.08mm 2P Male
Conector P2.54mm 2P Male
C_0603_1608Metric x 6
Bobinado
Carrete
Nucleo
Toroide - P7.68mm
SOIC-16_3.9x9.9mm_P1.27mm
TO-220-2_Horizontal_TabUp x 3
SOIC-8_3.9x4.9mm_P1.27mm
TO-220-3_Horizontal_TabUp x 5
DIP-4_W7.62mm_SMDSocket x 2
VFD_V1 1.54.1 x 2
D_MiniMELF
VFD_V1_PCB_1
VFD_V1_PCB_2
VFD_V1_PCB_3

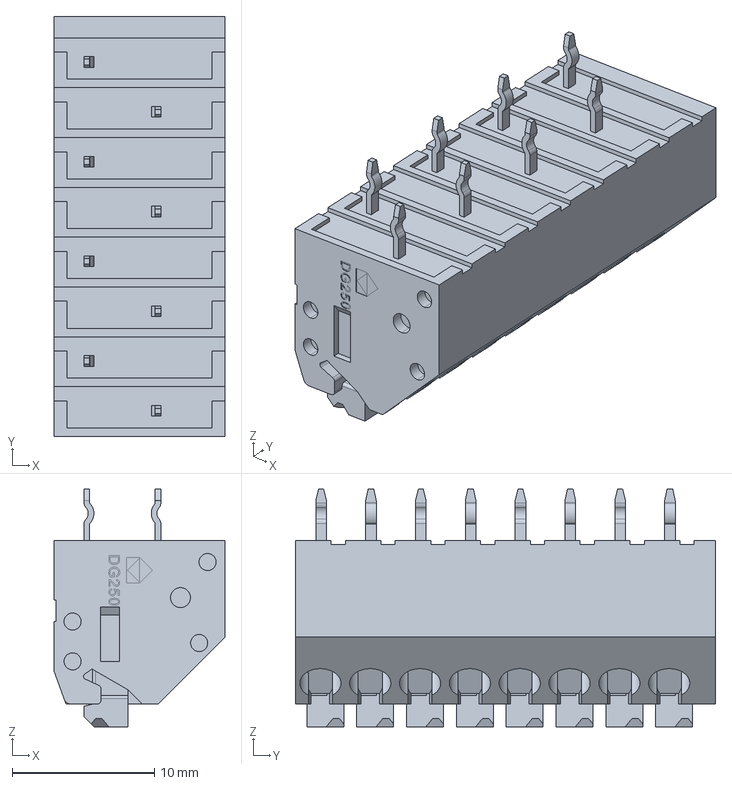
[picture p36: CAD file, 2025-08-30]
Hardware/PCB_MicroHMI/3DModels/DG250-3.5-08P-11-00A&Z(H).stp
12.0 x 29.5 x 16.7 mm

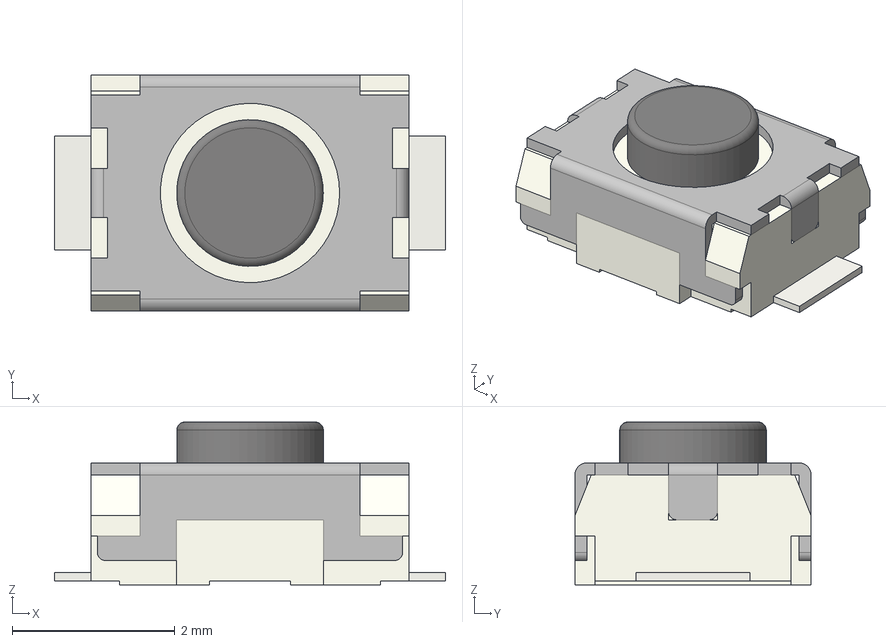
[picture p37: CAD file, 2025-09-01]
Modelo3D/SW_Push_SPST_NO_Alps_SKRK.step
4.80 x 2.90 x 2.00 mm

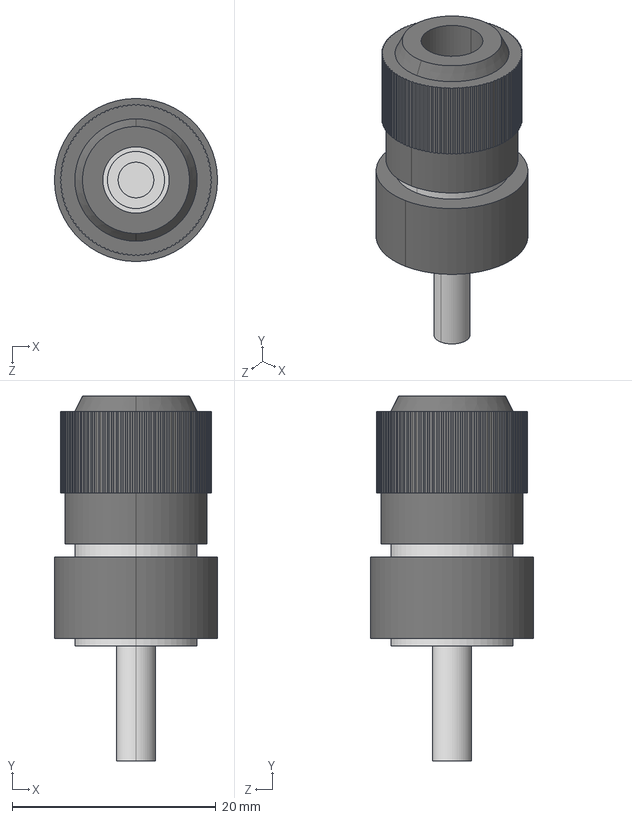
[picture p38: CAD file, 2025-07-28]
Hardware/PCB_Integradora/Modelos/Conectores/Conector Banana Socket 1P Negro.step
16.0 x 35.8 x 16.0 mm

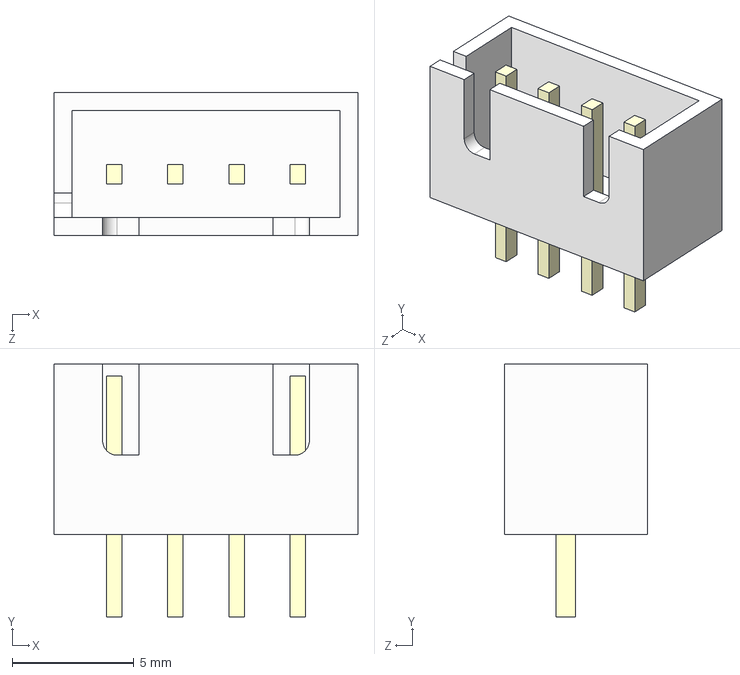
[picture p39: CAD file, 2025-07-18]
Hardware/PCB_Inversor/Modelos/Conectores/Conector P2.54mm 4P Male.step
12.5 x 10.4 x 5.90 mm

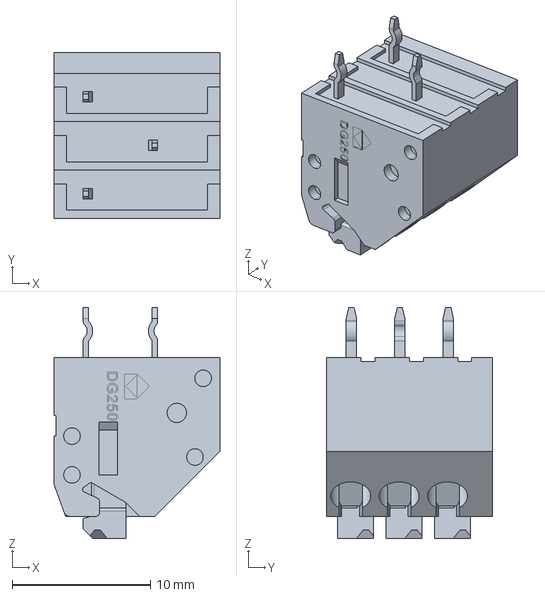
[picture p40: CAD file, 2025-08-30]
Hardware/PCB_MicroHMI/3DModels/DG250-3.5-03P-11-00A&Z(H).stp
12.0 x 12.0 x 16.7 mm

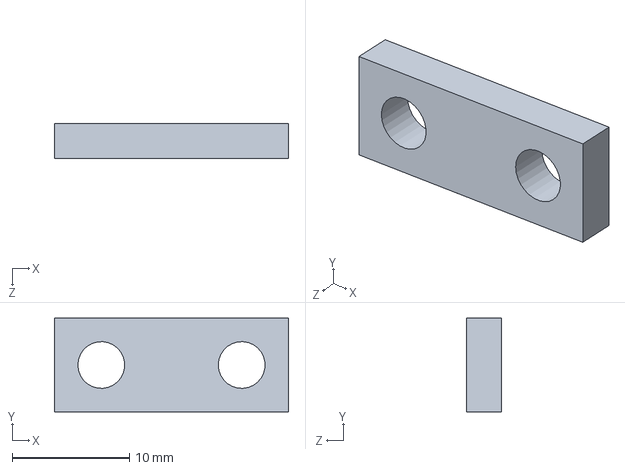
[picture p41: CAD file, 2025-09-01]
Modelo3D/SoporteDisipador.SLDPRT
20.0 x 8.00 x 3.00 mm

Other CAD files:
Hardware/PCB_Integradora/Modelos/Conectores/Conector Banana Socket 1P Rojo.step
Modelo3D/Soporte display.sldprt
Hardware/PCB_Integradora/Modelos/Conectores/Conector P5.08mm 3P Male.step
Hardware/PCB_Integradora/Modelos/Conectores/Conector P2.54mm 2P Male.step
Modelo3D/Bornera3P.SLDPRT
Modelo3D/Bornera8P.SLDPRT
Modelo3D/Boton.SLDPRT
Modelo3D/Cobertor interno.SLDPRT
Modelo3D/ConverterPCB.step
Modelo3D/Cooler.SLDPRT
Modelo3D/Covertor bornera.sldprt
Modelo3D/CovertorFrontal.SLDPRT
Modelo3D/Cuerpo.SLDPRT
Modelo3D/Difusor.SLDPRT
Modelo3D/Disipador.SLDPRT
Modelo3D/InterfacePCB.sldprt
Modelo3D/InterfacePCB.step
Modelo3D/InverterPCB.sldprt
Modelo3D/InverterPCB.step
Modelo3D/PlacaConversor.SLDPRT
Modelo3D/TapaDesplazable.SLDPRT
Modelo3D/Tecla.SLDPRT
Modelo3D/TecladoPCB.sldprt
Modelo3D/Tornillo M4.sldprt
Modelo3D/VFD_V1_PCB_1(3).sldprt

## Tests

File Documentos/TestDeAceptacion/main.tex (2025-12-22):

\documentclass[a4paper,10pt]{article}

% Paquetes
\usepackage{pdflscape}
\usepackage{titlesec}
\usepackage{titling}
\usepackage{setspace}
\usepackage[hidelinks]{hyperref}
\usepackage{graphicx}
\usepackage{caption}
\usepackage{subcaption}
\usepackage{float}
\usepackage{xcolor}
\usepackage[affil-it]{authblk}
\usepackage{biblatex}
\usepackage{tabularx}
\usepackage{array}

% Idioma
\usepackage[spanish]{babel}
\usepackage[utf8]{inputenc}

% Configuraciones
\usepackage{newtxtext,newtxmath}
\hypersetup{
    colorlinks,
    linkcolor={red!50!black},
    citecolor={blue!50!black},
    urlcolor={blue!80!black}
}

\begin{document}
\begin{titlepage}
\centering
\begin{figure}[t]
	\centering
	
    \vspace{0.5cm}
\end{figure}%
	{\LARGE Proyecto Final\par}
    {\LARGE 2025\par}
	\vspace{1cm}
	{\huge\bfseries Controlador de motor trifásico para instalaciones de baja tensión\par}
	\vspace{1cm}
    {\LARGE Test de Aceptación\par}
    \vspace{1cm}
	{\Large\itshape Elian Andrenacci, Lucas Manuel Carra\par}
	\vfill
\end{titlepage}

\tableofcontents

\newpage
\section{Objeto del Documento}
\label{sec:0_objeto}
El presente documento tiene por objeto presentar los diferentes puntos para el ensayo de las pruebas que demuestran que el equipo cumple con sus especificaciones acordadas en el documento de Anteproyecto.

Ejecutando los ensayos detallados en las secciones siguientes, se podrá validar el correcto funcionamiento de las distintas etapas del sistema. Asimismo, se evalúan parámetros eléctricos relevantes tales como tensiones, corrientes, formas de onda, estabilidad del bus DC y comportamiento del sistema ante distintas condiciones de carga.

Los resultados obtenidos permitirán determinar el grado de cumplimiento de los objetivos planteados inicialmente, identificar limitaciones del diseño actual y establecer lineamientos claros para futuras mejoras y optimizaciones del equipo.

\newpage
\section{Identificación del Producto}
\label{sec:1_ident}

El producto bajo ensayo corresponde a un prototipo funcional de variador de frecuencia trifásico alimentado con corriente continua, desarrollado en el marco del presente proyecto de grado y conforme al alcance definido en la etapa de Anteproyecto.

El dispositivo que se ve en la figura~\ref{fig:Dispositivo} se diseñó para accionar motores asincrónicos trifásicos de hasta $1/3 HP$ ($240 W$) de potencia nominal, a partir de una fuente de alimentación de $12 VDC$, generando una salida trifásica de $220 Vac$ con frecuencia variable en el rango de $0 Hz$ a $150 Hz$.

\begin{figure}[H]
\centering
    
    \caption{Render del dispositivo bajo medición.}
\label{fig:Dispositivo}
\end{figure}

El sistema integra una etapa de conversión y elevación de tensión de corriente continua, una etapa inversora trifásica controlada digitalmente, y un sistema de control que permite la variación de la velocidad de giro del motor mediante el ajuste de la frecuencia de salida. El dispositivo contempla señales de control e interfaz típicas del ámbito industrial, tales como entrada analógica de 0–10 V para referencia de velocidad, parada de emergencia y selección de velocidades preconfiguradas mediante entradas digitales.

En cuanto a las capacidades de comunicación, el producto admite la incorporación de conectividad WiFi orientada a la configuración. No obstante, en el alcance de este proyecto dicha funcionalidad se limita a una red local, permitiendo únicamente la configuración del equipo en las cercanías del inversor, sin contemplar operación remota a través de internet.

El prototipo desarrollado representa una solución orientada a aplicaciones de campo donde se dispone de alimentación en baja tensión continua y se requiere el control de motores trifásicos de potencia moderada, priorizando la simplicidad del sistema, la funcionalidad básica de control y la posibilidad de futuras ampliaciones.

\newpage
\section{Elementos y Equipamiento Necesarios}
\label{sec:2_elementos}

Para la realización de los ensayos y pruebas descriptos en este documento fue necesario contar con el siguiente equipamiento:

\begin{itemize}
    \item Dos fuentes de alimentación DC regulada, capaz de suministrar hasta $12 Vdc$ y una corriente de 40A requerida por el sistema bajo ensayo.
    \item Fuente de alimentación DC de $12Vdc$ de $10A$ para alimentar la etapa lógica del equipo.
    \item Motor asincrónico de inducción trifásico utilizado como carga, con características compatibles con el rango de operación del variador.
    \item Multímetros digitales para medición de tensiones y corrientes en continua y alterna.
    \item Osciloscopio digital de al menos dos canales para la observación de formas de onda de tensión y corriente.
    \item Termocuplas y multimetros para la medición de la temperatura de trabajo.
    \item Resistencia Shunt de $1.5m\Omega$ y $0.1\Omega$ para la medición de corriente de entrada.
    \item Dispositivo de frenado del motor.
    \item Cables, conectores, protecciones y elementos auxiliares necesarios para una conexión segura del sistema.
\end{itemize}

Todo el equipamiento fue utilizado respetando las normas básicas de seguridad eléctrica y buenas prácticas de laboratorio.

\newpage
\section{Desarrollo del Ensayo}
\label{sec:3_de}

El desarrollo de los ensayos se estructuró en distintas etapas con el objetivo de validar el correcto funcionamiento del variador de frecuencia trifásico, así como caracterizar su desempeño eléctrico, funcional y térmico dentro del alcance definido para el proyecto.

En primer lugar, se realizaron ensayos funcionales orientados a verificar el accionamiento del motor trifásico, evaluando las condiciones de arranque, régimen permanente y detención para un amplio rango de frecuencias de salida. Posteriormente, se llevaron a cabo ensayos específicos sobre el esquema de modulación por vector espacial (SVM), analizando la integridad de las señales generadas, la simetría de los pulsos y el comportamiento del índice de modulación conforme a la estrategia $V/f$.

Finalmente, se realizaron ensayos de rendimiento y durabilidad, permitiendo cuantificar la eficiencia de las distintas etapas del sistema y evaluar su capacidad de operación continua bajo carga. 

Todos los ensayos se efectuaron en un banco de pruebas controlado, utilizando instrumentación adecuada y respetando las limitaciones propias del prototipo desarrollado.

\newpage
\subsection{Forma de Medición}
\label{sec:4_formas}

Las mediciones eléctricas se realizaron mediante instrumentación externa, complementadas con las lecturas internas provistas por el sistema de control y supervisión del variador. Para la medición de tensiones continuas y alternas se emplearon multímetros digitales, mientras que las formas de onda de tensión y corriente fueron observadas utilizando un osciloscopio digital.

La corriente de entrada del conversor fue medida de manera indirecta mediante resistencias shunt de bajo valor, registrando la caída de tensión sobre las mismas con el osciloscopio. Esta metodología permitió analizar tanto el valor RMS de la corriente como su comportamiento temporal, caracterizado por una forma de onda pulsante asociada a la conmutación del conversor.

En el caso del inversor, las mediciones directas de corriente de salida fueron descartadas a causa de la presencia de ruido y resultados no coherentes, consecuencia de la conmutación PWM debiendo utilizar una carga resistiva de valor conmocido durante la evaluación del rendimiento del inversor que permita estimar la potencia entregada a partir de la tensión de línea medida.

\newpage
\subsection{Condiciones Iniciales}
\label{sec:5_ci}

Previo a la ejecución de cada ensayo, el sistema fue inicializado bajo condiciones controladas. El variador fue alimentado mediante dos fuentes de $12V$ conectadas en paralelo para la etapa de potencia, mientras que una tercera fuente independiente se destinó exclusivamente a la electrónica de control, asegurando estabilidad y aislamiento entre ambos subsistemas.

El motor trifásico fue inicialmente ensayado en vacío o con carga mínima utilizando un conexionado como el de la figura~\ref{fig:DiagramaDeConexion}, permitiendo verificar el funcionamiento básico del sistema antes de aplicar mayores demandas de potencia. La frecuencia de salida se configuró inicialmente en valores bajos, incrementándose progresivamente durante los ensayos para evitar esfuerzos innecesarios sobre la etapa de potencia.

\begin{figure}[H]
\centering
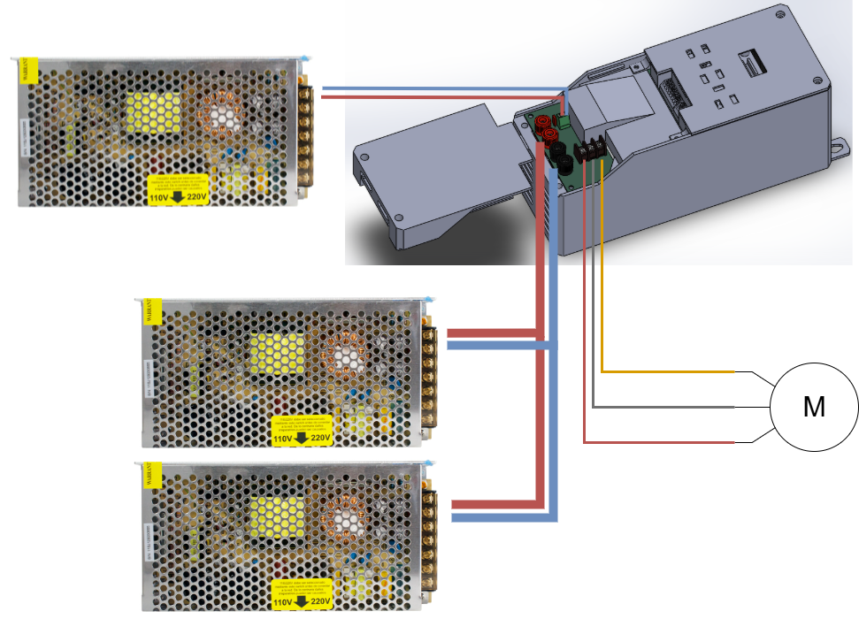
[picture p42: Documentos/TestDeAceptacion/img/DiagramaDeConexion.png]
    
    \caption{Diagrama de conexión de fuentes de alimentación y motor.}
\label{fig:DiagramaDeConexion}
\end{figure}

Asimismo, se verificó el correcto estado de las conexiones eléctricas, la inicialización del sistema de control y el correcto funcionamiento de las protecciones implementadas, incluyendo el circuito de parada de emergencia.

\newpage
\subsection{Preparación de la Prueba}
\label{sec:6_pprueba}

La preparación de cada prueba incluyó la configuración del banco de ensayos, la conexión del motor trifásico al inversor y la disposición de la instrumentación necesaria para la medición de las variables de interés.

Se establecieron puntos de medición para la tensión de salida donde marca la figura~\ref{fig:SalidaVAC}, de corriente de entrada con una resistencia de shunt en serie a las fuentes de tensión como se ve en la figura~\ref{fig:DiagramaDeConexionShunt} y la tensión y corriente en el bus DC como marca la figura~\ref{fig:DiagramaDeConexionVIdc}, considerando que la corriente máxima siempre sea menor a 2A.

\begin{figure}[H]
\centering
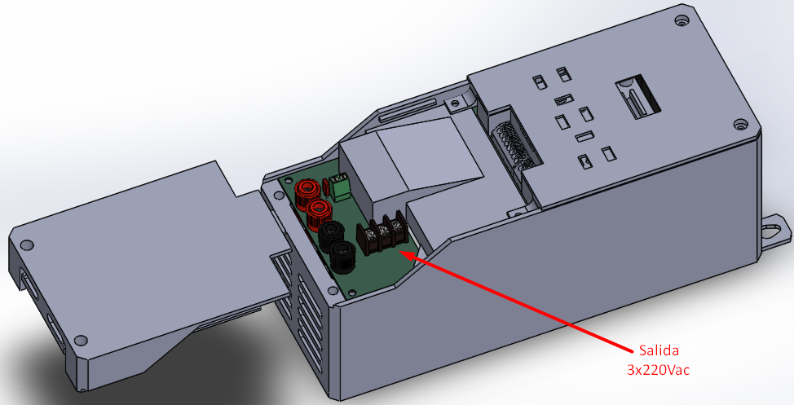
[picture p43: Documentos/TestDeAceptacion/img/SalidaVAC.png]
    
    \caption{Punto de medición de tensión de salida.}
\label{fig:SalidaVAC}
\end{figure}

\begin{figure}[H]
\centering
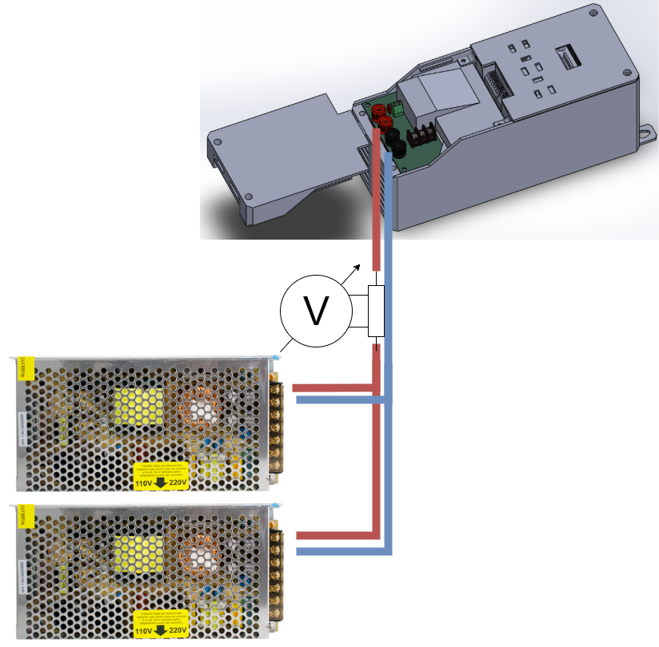
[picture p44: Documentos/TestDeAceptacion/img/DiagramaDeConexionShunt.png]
    
    \caption{Conexión para medición de corriente de entrada.}
\label{fig:DiagramaDeConexionShunt}
\end{figure}

\begin{figure}[H]
\centering
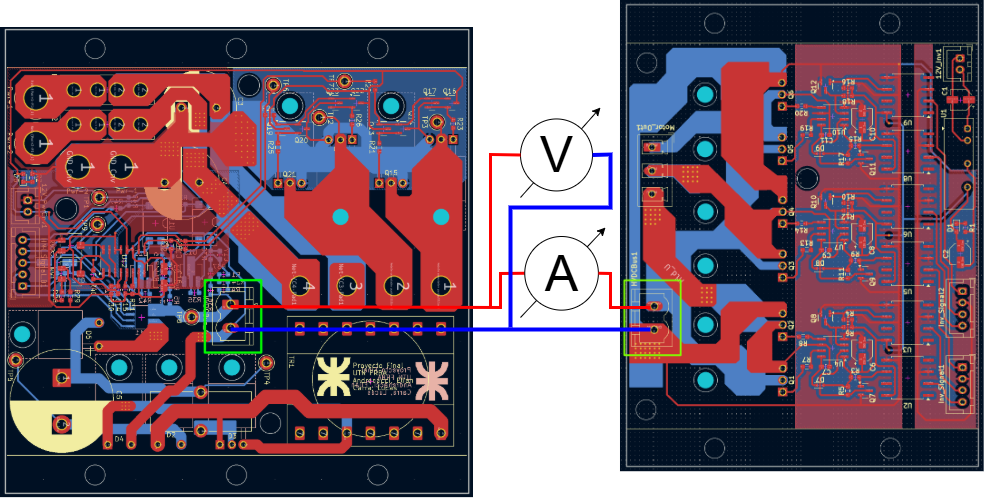
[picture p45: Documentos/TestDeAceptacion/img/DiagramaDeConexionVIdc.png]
    
    \caption{Punto de medición de tensión y corriente contínua del bus.}
\label{fig:DiagramaDeConexionVIdc}
\end{figure}

En los ensayos de modulación, se configuraron frecuencias de salida fijas y conocidas, permitiendo evaluar el comportamiento del sistema en distintos puntos de operación.

Para los ensayos de rendimiento, se montó el sistema de frenado dinámico sobre el motor observable en la figura~\ref{fig:FrenoMotor}, posibilitando la aplicación de distintos niveles de carga de manera controlada.

\begin{figure}[H]
\centering
    
    \caption{Freno dinámico sobre el motor.}
\label{fig:FrenoMotor}
\end{figure}

Antes de cada ensayo se verificó la correcta visualización de las magnitudes medidas en la interfaz del sistema, garantizando la coherencia entre las mediciones externas y las variables internas del variador.

\newpage
\subsection{Mediciones y Observaciones}
\label{sec:7_obs}

Durante los ensayos funcionales se observó un comportamiento estable del motor en todo el rango de frecuencias ensayado, comprendido entre $10Hz$ y $150Hz$, sin presencia de vibraciones, ruidos anómalos ni inestabilidades, indicando que el sistema trifásico generado por el inversor se encuentra correctamente balanceado y que el esquema de modulación implementado funciona conforme a lo esperado.

Los ensayos de modulación evidenciaron una correcta integridad de las señales generadas, con desfases adecuados entre fases y pulsos simétricos en los tiempos de conmutación. Se verificó en la figura~\ref{fig:v_f-vs-Freq} que el índice de modulación se ajusta correctamente a la estrategia $V/f$, manteniendo una relación proporcional entre la frecuencia de salida y la tensión aplicada al motor con una recta horizontal a lo largo de los diferentes puntos de operación. Esta condición también se puede observar en la figura~\ref{fig:Frecuencia-vs-Tension_AC}, que compara la tensión de salida contra la frecuencia de operación, donde se espera obtener una recta monótonamente creciente.

\begin{figure}[H]
\centering
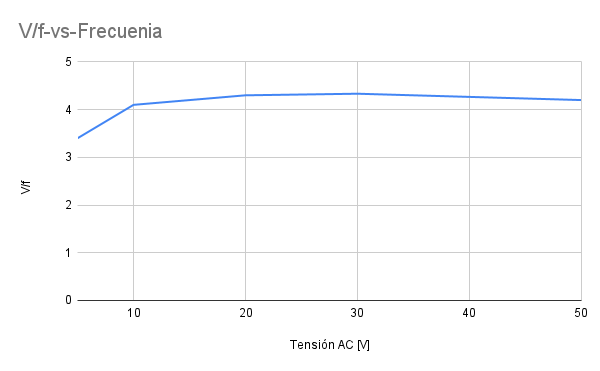
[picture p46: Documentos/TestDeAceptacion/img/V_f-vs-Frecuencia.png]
    
    \caption{Relación V/f frente a la frecuencia de operación.}
\label{fig:v_f-vs-Freq}
\end{figure}

\begin{figure}[H]
\centering
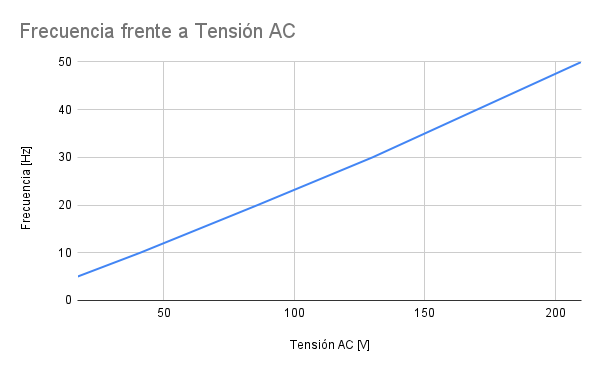
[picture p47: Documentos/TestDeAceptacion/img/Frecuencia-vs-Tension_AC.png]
    
    \caption{Relación frecuencia frente a la tensión de salida del dispositivo.}
\label{fig:Frecuencia-vs-Tension_AC}
\end{figure}

En cuanto al rendimiento, se observó que la etapa inversora presenta una eficiencia elevada $95.2\%$, mientras que la etapa conversora $85.4\%$, la cual constituye la principal fuente de pérdidas del sistema. Finalmente, durante los ensayos de durabilidad, se identificó una limitación térmica en el transformador del conversor, que restringe la potencia continua entregable a aproximadamente $1/6HP$ para una operación prolongada. Se puede ver en las figuras \ref{fig:Corriente} y \ref{fig:Tension} como los parámetros de salida se mantienen estables durante 30 minutos luego del transitorio del arranque.

\begin{figure}[H]
\centering
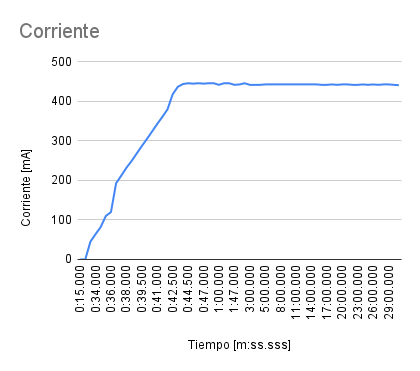
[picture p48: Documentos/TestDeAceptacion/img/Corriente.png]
    
    \caption{Evolución de la corriente durante 30 minutos de operación.}
\label{fig:Corriente}
\end{figure}

\begin{figure}[H]
\centering
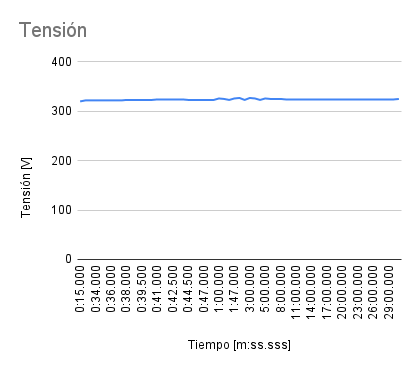
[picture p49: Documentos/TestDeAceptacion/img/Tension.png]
    
    \caption{Evolución de la tensión durante 30 minutos de operación.}
\label{fig:Tension}
\end{figure}

Además se evaluó el perfil de incremento de temperatura del transformador en la figura~\ref{fig:Temperatura} y, en las figuras~\ref{fig:Temperatura-vs-Corriente} y ~\ref{fig:Temperatura-vs-Tension} como las tensión y corriente del bus de contínua se mantienen estables durante toda la prueba frente a la variación de temperatura, al igual que la potencia sobre el motor como se ve en la figura~\ref{fig:Potencia}.

\begin{figure}[H]
\centering
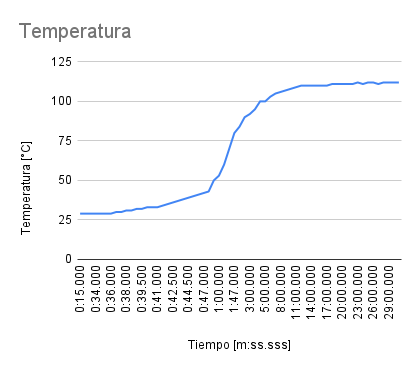
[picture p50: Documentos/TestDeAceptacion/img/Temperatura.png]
    
    \caption{Evolución de la temperatura durante 30 minutos de operación.}
\label{fig:Temperatura}
\end{figure}

\begin{figure}[H]
\centering
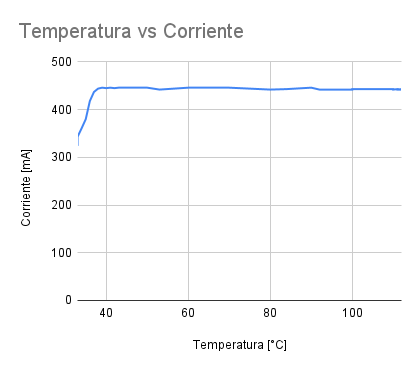
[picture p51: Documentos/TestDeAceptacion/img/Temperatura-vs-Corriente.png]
    
    \caption{Comparación temperatura vs corriente durante 30 minutos de operación.}
\label{fig:Temperatura-vs-Corriente}
\end{figure}

\begin{figure}[H]
\centering
    
    \caption{Comparación temperatura vs tensión durante 30 minutos de operación.}
\label{fig:Temperatura-vs-Tension}
\end{figure}

\begin{figure}[H]
\centering
    
    \caption{Evaluación de la potencia de salida durante 30 minutos de operación.}
\label{fig:Potencia}
\end{figure}

Se comprobó el correcto funcionamiento de la salida analógica de 0-10V, donde expone un funcionamiento lineal en la zona de frecuencias medias y una pequeña alinealidad en los extremos como se ve en la figura~\ref{fig:0-10V}-

\begin{figure}[H]
\centering
    
    \caption{Evolución de la salida 0-10V en representación de la frecuencia.}
\label{fig:0-10V}
\end{figure}

\newpage
\section{Conclusiones}
\label{sec:8_concl}

A partir de los ensayos realizados se concluye que el variador de frecuencia desarrollado cumple con los objetivos funcionales planteados en el alcance del proyecto, permitiendo el accionamiento y control de velocidad de un motor trifásico mediante una alimentación de baja tensión continua.

El sistema demuestra un funcionamiento estable, una modulación adecuada y un elevado rendimiento en la etapa inversora. No obstante, se identifican limitaciones en la etapa conversora, principalmente asociadas al diseño del transformador, condicionando la potencia continua máxima entregable y el comportamiento térmico del equipo.

En este sentido, el prototipo constituye una base sólida para futuras mejoras, orientadas a optimizar el diseño del conversor, incrementar la potencia continua y mejorar la robustez térmica del sistema, consolidando así una solución viable para aplicaciones reales dentro del dominio planteado.

Se detalla en la tabla~\ref{tab:resultados} cual fue el resultado de cada ensayo realizado:

\newpage
\begin{landscape}
    \begin{table}[H]
    \begin{tabular}{|l|l|c|c|c|}
    \hline
    \textbf{Ensayo}	& \textbf{Condición}                & \textbf{Resultado esperado}                                       & \textbf{Resultado obtenido}                   & \textbf{Estado} \\
    \hline
    Funcional       & 1/3HP 50Hz                        & Arranque y parada suave                                           & Mantenimiento de la relación V/f              & PASS \\
    \hline
    Funcional       & 1/3HP 50Hz                        & Arranque programado                                               & Arranque exitoso                              & PASS \\
    \hline
    Funcional       & 1/3HP 50Hz                        & Frenada programada                                                & Detención exitosa                             & PASS \\
    \hline
    Funcional       & 1/3HP 50Hz                        & Cambios de frecuencia de régimen, aceleración y desaceleración    & Parámetros configurados exitosamente          & PASS \\
    \hline
    Funcional       & 1/3HP 50Hz                        & Corte de seguridad por consumo de corriente alto                  & Corte por emergencia                          & PASS \\
    \hline
    Funcional       & 1/3HP 50Hz                        & Corte de seguridad por descenso de tensión excesivo               & Corte por emergencia                          & PASS \\
    \hline
    Funcional       & 1/3HP 50Hz                        & Cambio de velocidad durante el giro por cambio de entrada digital & Cambio de velocidad durante operación         & PASS \\
    \hline
    Funcional       & 1/3HP 50Hz                        & Indicación de frecuencia de operación en salida analógica 0-10V   & Curva V/f lineal en gran rango de operación   & PASS \\
    \hline
    Funcional       & 1/3HP 50Hz                        & Configuración por red Wi-Fi AP                                    & Parámetros configurados exitosamente          & PASS \\
    \hline
    Funcional       & 1/3HP 50Hz                        & Manipulación del motor por red Wi-FI AP                           & Arranque y parada exito                       & PASS \\
    \hline
    Durabilidad     & 1/3HP 10 min - Carga resistivas   & Sin fallas                                                        & Sobrecalientamiento Transformador $T_1$       & FAIL \\
    \hline
    Durabilidad     & 1/6HP 30 min - Carga resistivas   & Sin fallas                                                        & Funcionamiento estable y duradero             & PASS \\
    \hline
    Rendimiento     & 1/6HP 50Hz                        & $\eta_{Inversor} \ge 90\%$                                        & $\eta_{Inversor} \simeq 95.2\%$               & PASS \\
    \hline
    Rendimiento     & 1/3HP 50Hz                        & $\eta_{Convertidor} \ge 80\%$                                     & $\eta_{Convertidor} \simeq 85.4\%$            & PASS \\
    \hline
    \end{tabular}
    \caption{Resultado de las pruebas realizadas}
    \label{tab:resultados}
    \end{table}
\end{landscape}

\end{document}

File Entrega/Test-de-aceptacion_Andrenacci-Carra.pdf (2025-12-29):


# Proyecto Final

2025

# Controlador de motor trifasico para ´ instalaciones de baja tension´

# Test de Aceptacion´

## Elian Andrenacci, Lucas Manuel Carra

## Índice

1. Objeto del Documento | 2
2. Identificacion del Producto ´ | 3
3. Elementos y Equipamiento Necesarios | 4
4. Desarrollo del Ensayo | 5
5. Conclusiones | 15

1

## 1. Objeto del Documento

El presente documento tiene por objeto presentar los diferentes puntos para el ensayo de las pruebas que demuestran que el equipo cumple con sus especificaciones acordadas en el documento de Anteproyecto.
Ejecutando los ensayos detallados en las secciones siguientes, se podra validar ´ el correcto funcionamiento de las distintas etapas del sistema. Asimismo, se evalúan
parametros el ´ | ectricos relevantes tales como tensiones, corrientes, formas de onda, ´
estabilidad del bus DC y comportamiento del sistema ante distintas condiciones de carga.
Los resultados obtenidos permitiran determinar el grado de cumplimiento de los ´ objetivos planteados inicialmente, identificar limitaciones del diseno actual y establecer ˜ lineamientos claros para futuras mejoras y optimizaciones del equipo.

2

## 2. Identificacion del Producto ´

El producto bajo ensayo corresponde a un prototipo funcional de variador de frecuencia trifasico alimentado con corriente continua, desarrollado en el marco del presente ´ proyecto de grado y conforme al alcance definido en la etapa de Anteproyecto.
El dispositivo que se ve en la figura 1 se disenõ para accionar motores asincr ´ | onicos ´
trifasicos de hasta 1 ´ | /3HP (240W) de potencia nominal, a partir de una fuente de
alimentacion de 12 ´ | V DC, generando una salida trifasica de 220 ´ | V ac con frecuencia
variable en el rango de 0Hz a 150Hz.


Figura 1: Render del dispositivo bajo medicion. ´

El sistema integra una etapa de conversion y elevaci ´ | on de tensi ´ | on de corriente ´
continua, una etapa inversora trifasica controlada digitalmente, y un sistema de control ´ que permite la variacion de la velocidad de giro del motor mediante el ajuste de la ´
frecuencia de salida. El dispositivo contempla senales de control e interfaz t ˜ | ípicas del
ambito industrial, tales como entrada anal ´ | ogica de 0–10 V para referencia de velocidad, ´
parada de emergencia y seleccion de velocidades preconfiguradas mediante entradas ´ digitales.
En cuanto a las capacidades de comunicacion, el producto admite la incorporaci ´ | on´
de conectividad WiFi orientada a la configuracion. No obstante, en el alcance de este ´ proyecto dicha funcionalidad se limita a una red local, permitiendo únicamente la
configuracion del equipo en las cercan ´ | ías del inversor, sin contemplar operacion remota ´
a traves de internet. ´
El prototipo desarrollado representa una solucion orientada a aplicaciones de campo ´
donde se dispone de alimentacion en baja tensi ´ | on continua y se requiere el control de ´
motores trifasicos de potencia moderada, priorizando la simplicidad del sistema, la ´ funcionalidad basica de control y la posibilidad de futuras ampliaciones. ´

3

## 3. Elementos y Equipamiento Necesarios

Para la realizacion de los ensayos y pruebas descriptos en este documento fue ´ necesario contar con el siguiente equipamiento:

Dos fuentes de alimentacion DC regulada, capaz de suministrar hasta 12 ´ | | | V dc y
una corriente de 40A requerida por el sistema bajo ensayo.
Fuente de alimentacion DC de 12 ´ | | V dc de 10A para alimentar la etapa logica del ´
equipo.
Motor asincronico de inducci ´ | on trif ´ | asico utilizado como carga, con caracter ´ | ísticas
compatibles con el rango de operacion del variador. ´

Multímetros digitales para medicion de tensiones y corrientes en continua y ´ alterna.

Osciloscopio digital de al menos dos canales para la observacion de formas de ´ onda de tension y corriente. ´

Termocuplas y multimetros para la medicion de la temperatura de trabajo. ´

Resistencia Shunt de 1,5mΩ y 0,1Ω para la medicion de corriente de entrada. ´

Dispositivo de frenado del motor.

Cables, conectores, protecciones y elementos auxiliares necesarios para una conexion segura del sistema. ´

Todo el equipamiento fue utilizado respetando las normas basicas de seguridad ´
electrica y buenas pr ´ | acticas de laboratorio. ´

4

## 4. Desarrollo del Ensayo

El desarrollo de los ensayos se estructuro en distintas etapas con el objetivo de validar ´
el correcto funcionamiento del variador de frecuencia trifasico, as ´ | í como caracterizar su
desempeno el ˜ | ectrico, funcional y t ´ | ermico dentro del alcance definido para el proyecto. ´
En primer lugar, se realizaron ensayos funcionales orientados a verificar el acciona-
miento del motor trifasico, evaluando las condiciones de arranque, r ´ | egimen permanente ´
y detencion para un amplio rango de frecuencias de salida. Posteriormente, se lleva- ´ ron a cabo ensayos específicos sobre el esquema de modulacion por vector espacial ´
(SVM), analizando la integridad de las senales generadas, la simetr ˜ | ía de los pulsos y el
comportamiento del índice de modulacion conforme a la estrategia ´ | V/ f .
Finalmente, se realizaron ensayos de rendimiento y durabilidad, permitiendo cuantificar la eficiencia de las distintas etapas del sistema y evaluar su capacidad de operacion´ continua bajo carga.
Todos los ensayos se efectuaron en un banco de pruebas controlado, utilizando instrumentacion adecuada y respetando las limitaciones propias del prototipo desarrollado. ´

5

### 4.1. Forma de Medicion´

Las mediciones electricas se realizaron mediante instrumentaci ´ | on externa, comple- ´
mentadas con las lecturas internas provistas por el sistema de control y supervision del ´
variador. Para la medicion de tensiones continuas y alternas se emplearon mult ´ | ímetros
digitales, mientras que las formas de onda de tension y corriente fueron observadas ´ utilizando un osciloscopio digital.
La corriente de entrada del conversor fue medida de manera indirecta mediante resistencias shunt de bajo valor, registrando la caída de tension sobre las mismas con ´ el osciloscopio. Esta metodología permitio analizar tanto el valor RMS de la corriente ´ como su comportamiento temporal, caracterizado por una forma de onda pulsante asociada a la conmutacion del conversor. ´
En el caso del inversor, las mediciones directas de corriente de salida fueron descartadas a causa de la presencia de ruido y resultados no coherentes, consecuencia de la conmutacion PWM debiendo utilizar una carga resistiva de valor conmocido durante ´ la evaluacion del rendimiento del inversor que permita estimar la potencia entregada a ´ partir de la tension de l ´ ínea medida.

6

### 4.2. Condiciones Iniciales

Previo a la ejecucion de cada ensayo, el sistema fue inicializado bajo condiciones ´ controladas. El variador fue alimentado mediante dos fuentes de 12V conectadas en paralelo para la etapa de potencia, mientras que una tercera fuente independiente se
destino exclusivamente a la electr ´ | onica de control, asegurando estabilidad y aislamiento ´
entre ambos subsistemas.
El motor trifasico fue inicialmente ensayado en vac ´ | ío o con carga mínima utilizando
un conexionado como el de la figura 2, permitiendo verificar el funcionamiento basico ´ del sistema antes de aplicar mayores demandas de potencia. La frecuencia de salida se
configuro inicialmente en valores bajos, increment ´ | andose progresivamente durante los ´
ensayos para evitar esfuerzos innecesarios sobre la etapa de potencia.


Figura 2: Diagrama de conexion de fuentes de alimentaci ´ | on y motor. ´
Asimismo, se verifico el correcto estado de las conexiones el ´ | ectricas, la inicializa- ´
cion del sistema de control y el correcto funcionamiento de las protecciones implemen- ´ tadas, incluyendo el circuito de parada de emergencia.

7

### 4.3. Preparacion de la Prueba ´

La preparacion de cada prueba incluy ´ | o la configuraci ´ | on del banco de ensayos, la ´
conexion del motor trif ´ | asico al inversor y la disposici ´ | on de la instrumentaci ´ | on necesaria ´
para la medicion de las variables de inter ´ | es. ´
Se establecieron puntos de medicion para la tensi ´ | on de salida donde marca la ´
figura 3, de corriente de entrada con una resistencia de shunt en serie a las fuentes de
tension como se ve en la figura ´ | 4 y la tension y corriente en el bus DC como marca la ´
figura 5, considerando que la corriente maxima siempre sea menor a 2A. ´


Figura 3: Punto de medicion de tensi ´ | on de salida. ´


Figura 4: Conexion para medici ´ | on de corriente de entrada. ´

8


Figura 5: Punto de medicion de tensi ´ | on y corriente cont ´ | ínua del bus.

En los ensayos de modulacion, se configuraron frecuencias de salida fijas y co- ´ nocidas, permitiendo evaluar el comportamiento del sistema en distintos puntos de operacion. ´
Para los ensayos de rendimiento, se monto el sistema de frenado din ´ | amico sobre el ´
motor observable en la figura 6, posibilitando la aplicacion de distintos niveles de carga ´ de manera controlada.


Figura 6: Freno dinamico sobre el motor. ´

Antes de cada ensayo se verifico la correcta visualizaci ´ | on de las magnitudes medidas ´
en la interfaz del sistema, garantizando la coherencia entre las mediciones externas y las variables internas del variador.

9

### 4.4. Mediciones y Observaciones

Durante los ensayos funcionales se observo un comportamiento estable del motor en ´ todo el rango de frecuencias ensayado, comprendido entre 10Hz y 150Hz, sin presencia
de vibraciones, ruidos anomalos ni inestabilidades, indicando que el sistema trif ´ | asico ´
generado por el inversor se encuentra correctamente balanceado y que el esquema de modulacion implementado funciona conforme a lo esperado. ´
Los ensayos de modulacion evidenciaron una correcta integridad de las se ´ | nales ˜
generadas, con desfases adecuados entre fases y pulsos simetricos en los tiempos ´
de conmutacion. Se verific ´ | o en la figura ´ | 7 que el índice de modulacion se ajusta ´
correctamente a la estrategia V/ f , manteniendo una relacion proporcional entre la ´ frecuencia de salida y la tension aplicada al motor con una recta horizontal a lo largo ´
de los diferentes puntos de operacion. Esta condici ´ | on tambi ´ | en se puede observar en la ´
figura 8, que compara la tension de salida contra la frecuencia de operaci ´ | on, donde se ´
espera obtener una recta monotonamente creciente. ´


Figura 7: Relacion V/f frente a la frecuencia de operaci ´ | on. ´


Figura 8: Relacion frecuencia frente a la tensi ´ | on de salida del dispositivo. ´

En cuanto al rendimiento, se observo que la etapa inversora presenta una eficiencia ´ elevada 95,2 %, mientras que la etapa conversora 85,4 %, la cual constituye la principal fuente de perdidas del sistema. Finalmente, durante los ensayos de durabilidad, se ´

10

identifico una limitaci ´ | on t ´ ermica en el transformador del conversor, que restringe la po- ´
tencia continua entregable a aproximadamente 1/6HP para una operacion prolongada. ´ Se puede ver en las figuras 9 y 10 como los parametros de salida se mantienen estables ´ durante 30 minutos luego del transitorio del arranque.


Figura 9: Evolucion de la corriente durante 30 minutos de operaci ´ | on. ´


Figura 10: Evolucion de la tensi ´ | on durante 30 minutos de operaci ´ | on. ´
Ademas se evalu ´ | o el perfil de incremento de temperatura del transformador en la ´
figura 11 y, en las figuras 12 y 13 como las tension y corriente del bus de cont ´ | ínua se

11 mantienen estables durante toda la prueba frente a la variacion de temperatura, al igual ´ que la potencia sobre el motor como se ve en la figura 14.


Figura 11: Evolucion de la temperatura durante 30 minutos de operaci ´ | on. ´


Figura 12: Comparacion temperatura vs corriente durante 30 minutos de operaci ´ | on. ´

12


Figura 13: Comparacion temperatura vs tensi ´ | on durante 30 minutos de operaci ´ | on. ´


Figura 14: Evaluacion de la potencia de salida durante 30 minutos de operaci ´ | on. ´
Se comprobo el correcto funcionamiento de la salida anal ´ | ogica de 0-10V, donde ´
expone un funcionamiento lineal en la zona de frecuencias medias y una pequenã alinealidad en los extremos como se ve en la figura 15-

13


Figura 15: Evolucion de la salida 0-10V en representaci ´ | on de la frecuencia. ´

14

## 5. Conclusiones

A partir de los ensayos realizados se concluye que el variador de frecuencia desarrollado cumple con los objetivos funcionales planteados en el alcance del proyecto, permitiendo el accionamiento y control de velocidad de un motor trifasico mediante ´
una alimentacion de baja tensi ´ | on continua. ´
El sistema demuestra un funcionamiento estable, una modulacion adecuada y un ´ elevado rendimiento en la etapa inversora. No obstante, se identifican limitaciones en la etapa conversora, principalmente asociadas al diseno del transformador, condicionando ˜
la potencia continua maxima entregable y el comportamiento t ´ | ermico del equipo. ´
En este sentido, el prototipo constituye una base solida para futuras mejoras, orien- ´ tadas a optimizar el diseno del conversor, incrementar la potencia continua y mejorar ˜
la robustez termica del sistema, consolidando as ´ | í una solucion viable para aplicaciones ´
reales dentro del dominio planteado.
Se detalla en la tabla 1 cual fue el resultado de cada ensayo realizado:

15

Ensayo | Condicion´ | Resultado esperado | Resultado obtenido | Estado
Funcional | 1/3HP 50Hz | Arranque y parada suave | Mantenimiento de la relacion V/f ´ | PASS
Funcional | 1/3HP 50Hz | Arranque programado | Arranque exitoso | PASS
Funcional | 1/3HP 50Hz | Frenada programada | Detencion exitosa ´ | PASS
Funcional | 1/3HP 50Hz | Cambios de frecuencia de regimen, aceleraci ´ on y desaceleraci ´ on´ | Parametros configurados exitosamente ´ | PASS
Funcional | 1/3HP 50Hz | Corte de seguridad por consumo de corriente alto | Corte por emergencia | PASS
Funcional | 1/3HP 50Hz | Corte de seguridad por descenso de tension excesivo ´ | Corte por emergencia | PASS
Funcional | 1/3HP 50Hz | Cambio de velocidad durante el giro por cambio de entrada digital | Cambio de velocidad durante operacion´ | PASS
Funcional | 1/3HP 50Hz | Indicacion de frecuencia de operaci ´ on en salida anal ´ ogica 0-10V ´ | Curva V/f lineal en gran rango de operacion´ | PASS
Funcional | 1/3HP 50Hz | Configuracion por red Wi-Fi AP ´ | Parametros configurados exitosamente ´ | PASS
Funcional | 1/3HP 50Hz | Manipulacion del motor por red Wi-FI AP ´ | Arranque y parada exito | PASS
Durabilidad | 1/3HP 10 min - Carga resistivas | Sin fallas | Sobrecalientamiento Transformador T1 | FAIL
Durabilidad | 1/6HP 30 min - Carga resistivas | Sin fallas | Funcionamiento estable y duradero | PASS
Rendimiento | 1/6HP 50Hz | ηInver sor ≥ 90 % | ηInver sor ≃ 95,2 % | PASS
Rendimiento | 1/3HP 50Hz | ηConver t idor ≥ 80 % | ηConver t idor ≃ 85,4 % | PASS

Cuadro 1: Resultado de las pruebas realizadas

16

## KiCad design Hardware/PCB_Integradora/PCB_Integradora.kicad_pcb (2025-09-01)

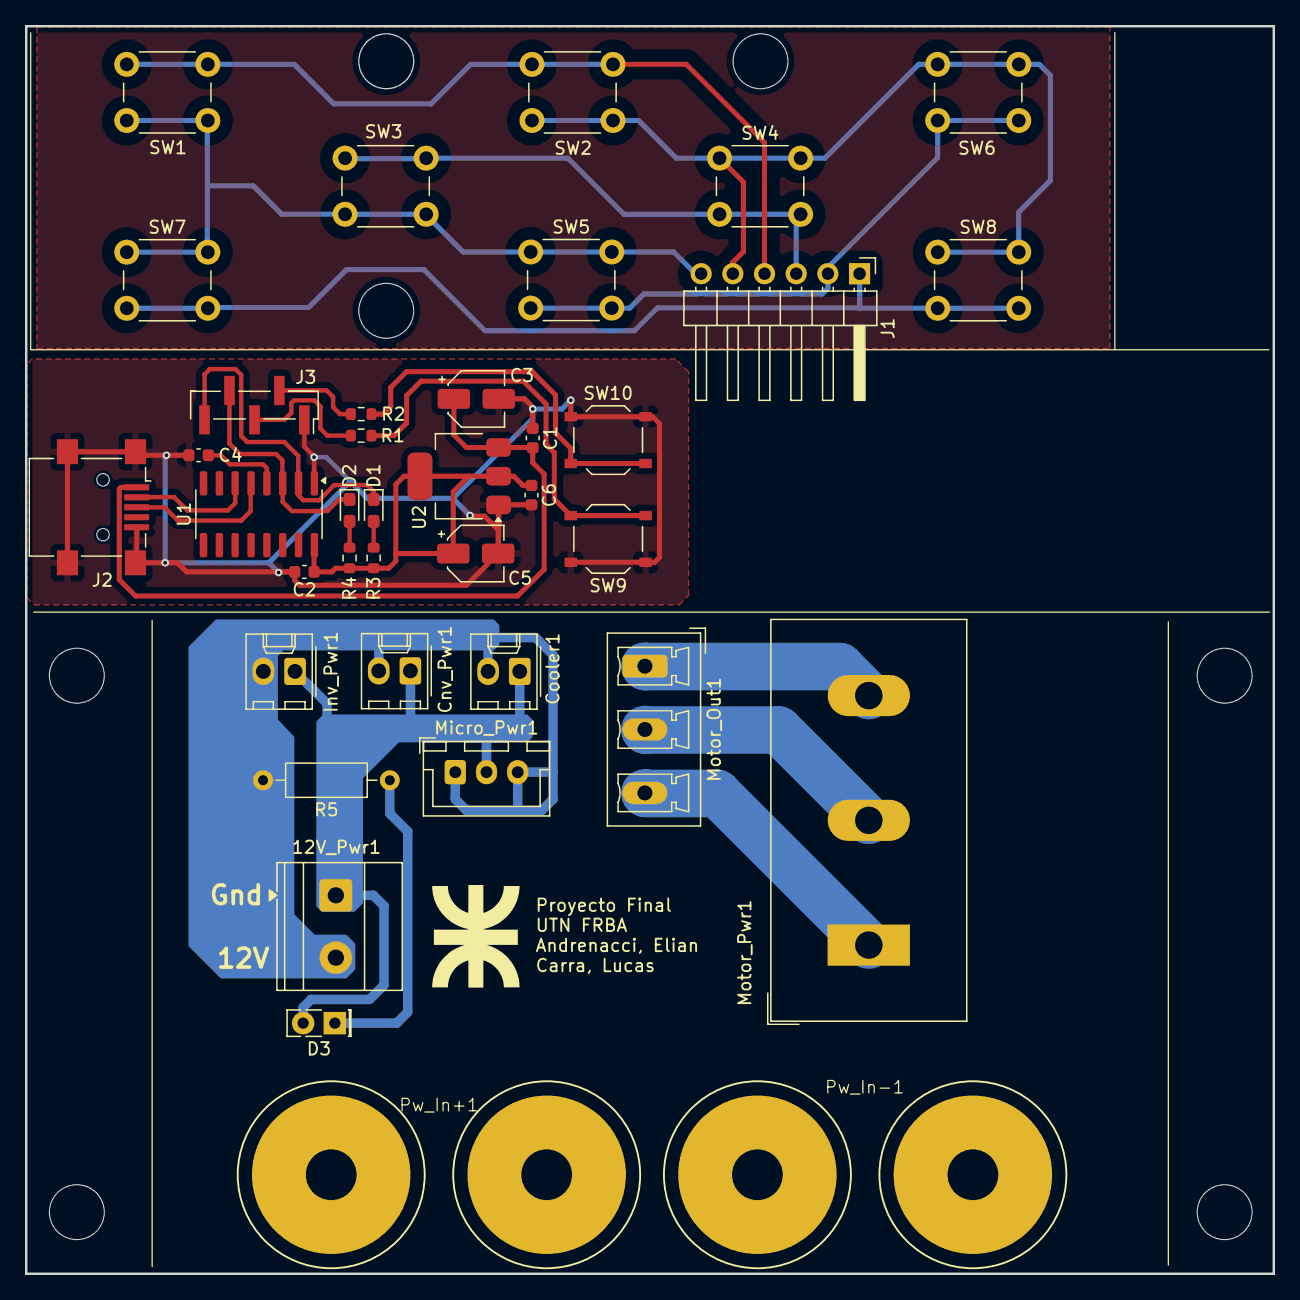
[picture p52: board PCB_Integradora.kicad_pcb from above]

Board: 2 copper layers, 100.0 x 100.0 mm, 38 parts (0 on the bottom side), 26 nets.

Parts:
12V_Pwr1: Screw_Terminal_01x02; TerminalBlock_Phoenix_MKDS-1,5-2_1x02_P5.00mm_Horizontal
C1, C6: 1uF; C_0603_1608Metric
C2, C4: 1nF; C_0603_1608Metric
C3: 10uF; CP_Elec_4x5.4
C5: 22uF; CP_Elec_4x5.4
Cnv_Pwr1: Conn_01x02; Molex_KK-254_AE-6410-02A_1x02_P2.54mm_Vertical
Cooler1: Conn_01x02; Molex_KK-254_AE-6410-02A_1x02_P2.54mm_Vertical
D1, D2: LED; LED_0603_1608Metric_Pad1.05x0.95mm_HandSolder
D3: LED_Green; LED_Rectangular_W5.0mm_H2.0mm
Inv_Pwr1: Conn_01x02; Molex_KK-254_AE-6410-02A_1x02_P2.54mm_Vertical
J1: Conn_01x06; PinHeader_1x06_P2.54mm_Horizontal
J2: USB_OTG; USB_Mini-B_Lumberg_2486_01_Horizontal
J3: Conn_01x05_Pin; PinHeader_1x05_P2.00mm_Vertical_SMD_Pin1Right
Micro_Pwr1: Conn_01x03; JST_XH_B3B-XH-A_1x03_P2.50mm_Vertical
Motor_Out1: Conn_01x03; PhoenixContact_MCV_1,5_3-G-5.08_1x03_P5.08mm_Vertical
Motor_Pwr1: Screw_Terminal_01x03; TerminalBlock_Dinkle_DT-55-B01X-03_P10.00mm
Pw_In+1: Conn_01x02; BananaSocket - 2P - 4mm
Pw_In-1: Conn_01x02; BananaSocket - 2P - 4mm
R1, R2, R3, R4: 221; R_0603_1608Metric
R5: 1.2k; R_Axial_DIN0207_L6.3mm_D2.5mm_P10.16mm_Horizontal
SW1, SW2, SW3, SW4, SW5, SW6, SW7, SW8: SW_Push; SW_PUSH_6mm
SW9, SW10: SW_MEC_5E; SW_Push_1P1T_XKB_TS-1187A
U1: CH340C; SOIC-16_3.9x9.9mm_P1.27mm
U2: AMS1117-3.3; SOT-223-3_TabPin2

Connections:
+3.3V: C2.1, C5.1, C6.1, R3.1, R4.1, U1.16 (VCC), U2.2 (VO)
+5V: C1.1, C3.1, J2.1 (VBUS), U2.3 (VI)
/ESP Programadora/BOOT_prog: J3.2, R2.1
/ESP Programadora/ENABLE: J3.3, R1.1
/ESP Programadora/Rx: D2.1 (K), J3.4, U1.3 (RXD)
/ESP Programadora/Tx: D1.1 (K), J3.5, U1.2 (TXD)
/Interfaz HMI/Matrix_0: J1.1, SW7.2, SW8.2
/Interfaz HMI/Matrix_1: J1.2, SW5.2, SW6.2
/Interfaz HMI/Matrix_2: J1.3, SW3.2, SW4.2
/Interfaz HMI/Matrix_3: J1.4, SW1.2, SW2.2
/Interfaz HMI/Matrix_4: J1.5, SW2.1, SW4.1, SW6.1, SW8.1
/Interfaz HMI/Matrix_5: J1.6, SW1.1, SW3.1, SW5.1, SW7.1
/Interfaz de conexión/12V_Cnv: 12V_Pwr1.1, Cnv_Pwr1.1, Cooler1.1, D3.2 (A), Inv_Pwr1.1, Micro_Pwr1.2
/Interfaz de conexión/Gnd_Cnv: 12V_Pwr1.2, Cnv_Pwr1.2, Cooler1.2, Inv_Pwr1.2, Micro_Pwr1.1, Micro_Pwr1.3, R5.2
GND: C1.2, C2.2, C3.2, C4.1, C5.2, C6.2, J2.5 (GND), J2.6 (Shield), J3.1, SW9.1, SW9.2, SW10.1, SW10.2, U1.1 (GND), U2.1 (GND)
unnamed: D1.2 (A), R3.2
unnamed: D2.2 (A), R4.2
unnamed: D3.1 (K), R5.1
unnamed: J2.3 (D+), U1.5 (UD+)
unnamed: J2.2 (D-), U1.6 (UD-)
unnamed: Motor_Out1.1, Motor_Pwr1.3
unnamed: Motor_Out1.2, Motor_Pwr1.2
unnamed: Motor_Out1.3, Motor_Pwr1.1
unnamed: R1.2, SW9.3 (K), SW9.4 (A)
unnamed: R2.2, SW10.3 (K), SW10.4 (A)
unnamed: C4.2, U1.4 (V3)

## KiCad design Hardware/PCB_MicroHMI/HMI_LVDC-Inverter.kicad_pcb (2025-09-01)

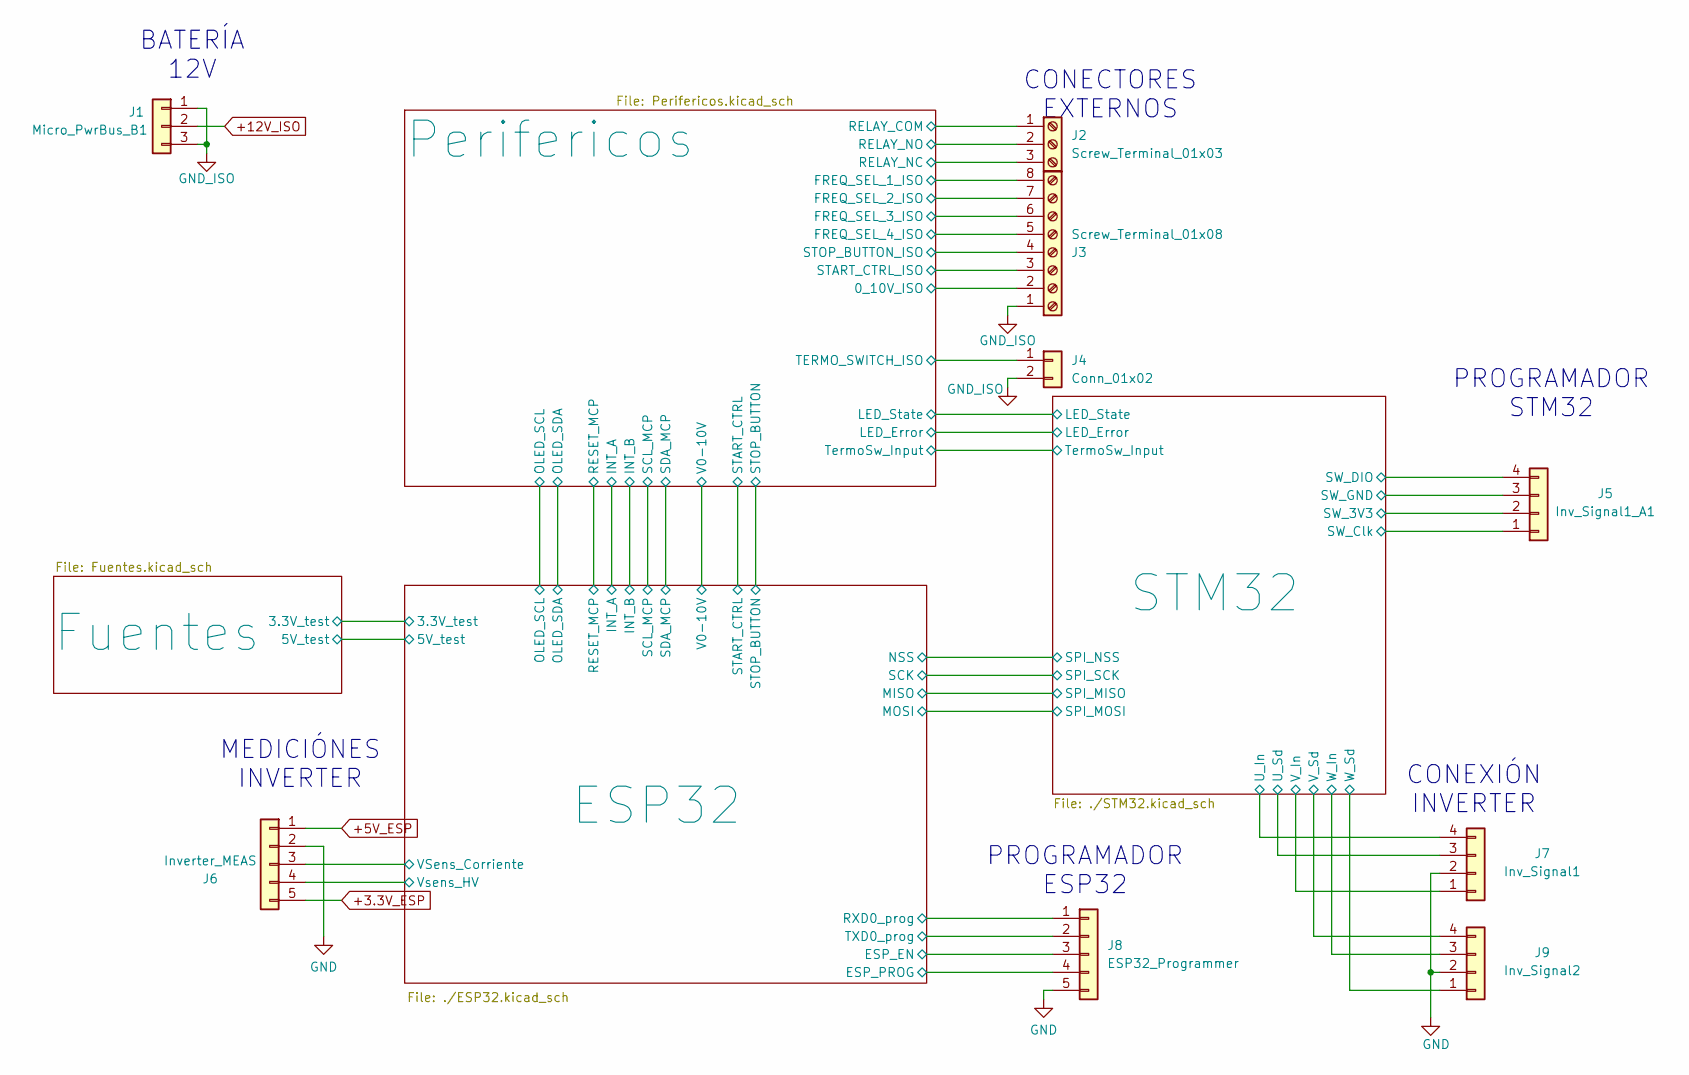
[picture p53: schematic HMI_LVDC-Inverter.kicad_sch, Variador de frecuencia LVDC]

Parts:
J1: Micro_PwrBus_B1; JST_XH_B3B-XH-A_1x03_P2.50mm_Vertical
J2: Screw_Terminal_01x03; TerminalBlock_Degson_DG250-3.5-03P_1x03_P3.50mm_45Degree
J3: Screw_Terminal_01x08; TerminalBlock_Degson_DG250-3.5-08P_1x08_P3.50mm_45Degree
J4: Conn_01x02; JST_XH_B2B-XH-A_1x02_P2.50mm_Vertical
J5: Inv_Signal1_A1; PinHeader_1x04_P2.54mm_Vertical
J6: Inverter_MEAS; JST_XH_B5B-XH-A_1x05_P2.50mm_Vertical
J7: Inv_Signal1; JST_XH_B4B-XH-A_1x04_P2.50mm_Vertical
J8: ESP32_Programmer; PinHeader_1x05_P2.54mm_Vertical
J9: Inv_Signal2; JST_XH_B4B-XH-A_1x04_P2.50mm_Vertical

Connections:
+3.3V_ESP: J6.5; also elsewhere on the board
+5V_ESP: J6.1; also elsewhere on the board
+12V_ISO: J1.2; also elsewhere on the board
/ESP32/BOOT_prog: J8.4; also elsewhere on the board
/ESP32/ENABLE: J8.3; also elsewhere on the board
/ESP32/RXD0_prog: J8.1; also elsewhere on the board
/ESP32/TXD0_prog: J8.2; also elsewhere on the board
/ESP32/VSens_Corriente: J6.3; also elsewhere on the board
/ESP32/Vsens_HV: J6.4; also elsewhere on the board
/Perifericos/0_10V_ISO: J3.2; also elsewhere on the board
/Perifericos/FREQ_SEL_1_ISO: J3.8; also elsewhere on the board
/Perifericos/FREQ_SEL_2_ISO: J3.7; also elsewhere on the board
/Perifericos/FREQ_SEL_3_ISO: J3.6; also elsewhere on the board
/Perifericos/FREQ_SEL_4_ISO: J3.5; also elsewhere on the board
/Perifericos/RELAY_COM: J2.1; also elsewhere on the board
/Perifericos/RELAY_NC: J2.3; also elsewhere on the board
/Perifericos/RELAY_NO: J2.2; also elsewhere on the board
/Perifericos/START_CTRL_ISO: J3.3; also elsewhere on the board
/Perifericos/STOP_BUTTON_ISO: J3.4; also elsewhere on the board
/Perifericos/TERMO_SWITCH_ISO: J4.1; also elsewhere on the board
/STM32/SW_3V3: J5.2; also elsewhere on the board
/STM32/SW_Clk: J5.1; also elsewhere on the board
/STM32/SW_DIO: J5.4; also elsewhere on the board
/STM32/U_In: J7.4; also elsewhere on the board
/STM32/U_Sd: J7.3; also elsewhere on the board
/STM32/V_In: J7.1; also elsewhere on the board
/STM32/V_Sd: J9.4; also elsewhere on the board
/STM32/W_In: J9.3; also elsewhere on the board
/STM32/W_Sd: J9.1; also elsewhere on the board
GND: J5.3, J6.2, J7.2, J8.5, J9.2; also elsewhere on the board
GND_ISO: J1.1, J1.3, J3.1, J4.2; also elsewhere on the board

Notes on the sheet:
CONEXIÓN INVERTER
PROGRAMADOR ESP32
PROGRAMADOR STM32
BATERÍA 12V
MEDICIÓNES INVERTER
CONECTORES EXTERNOS

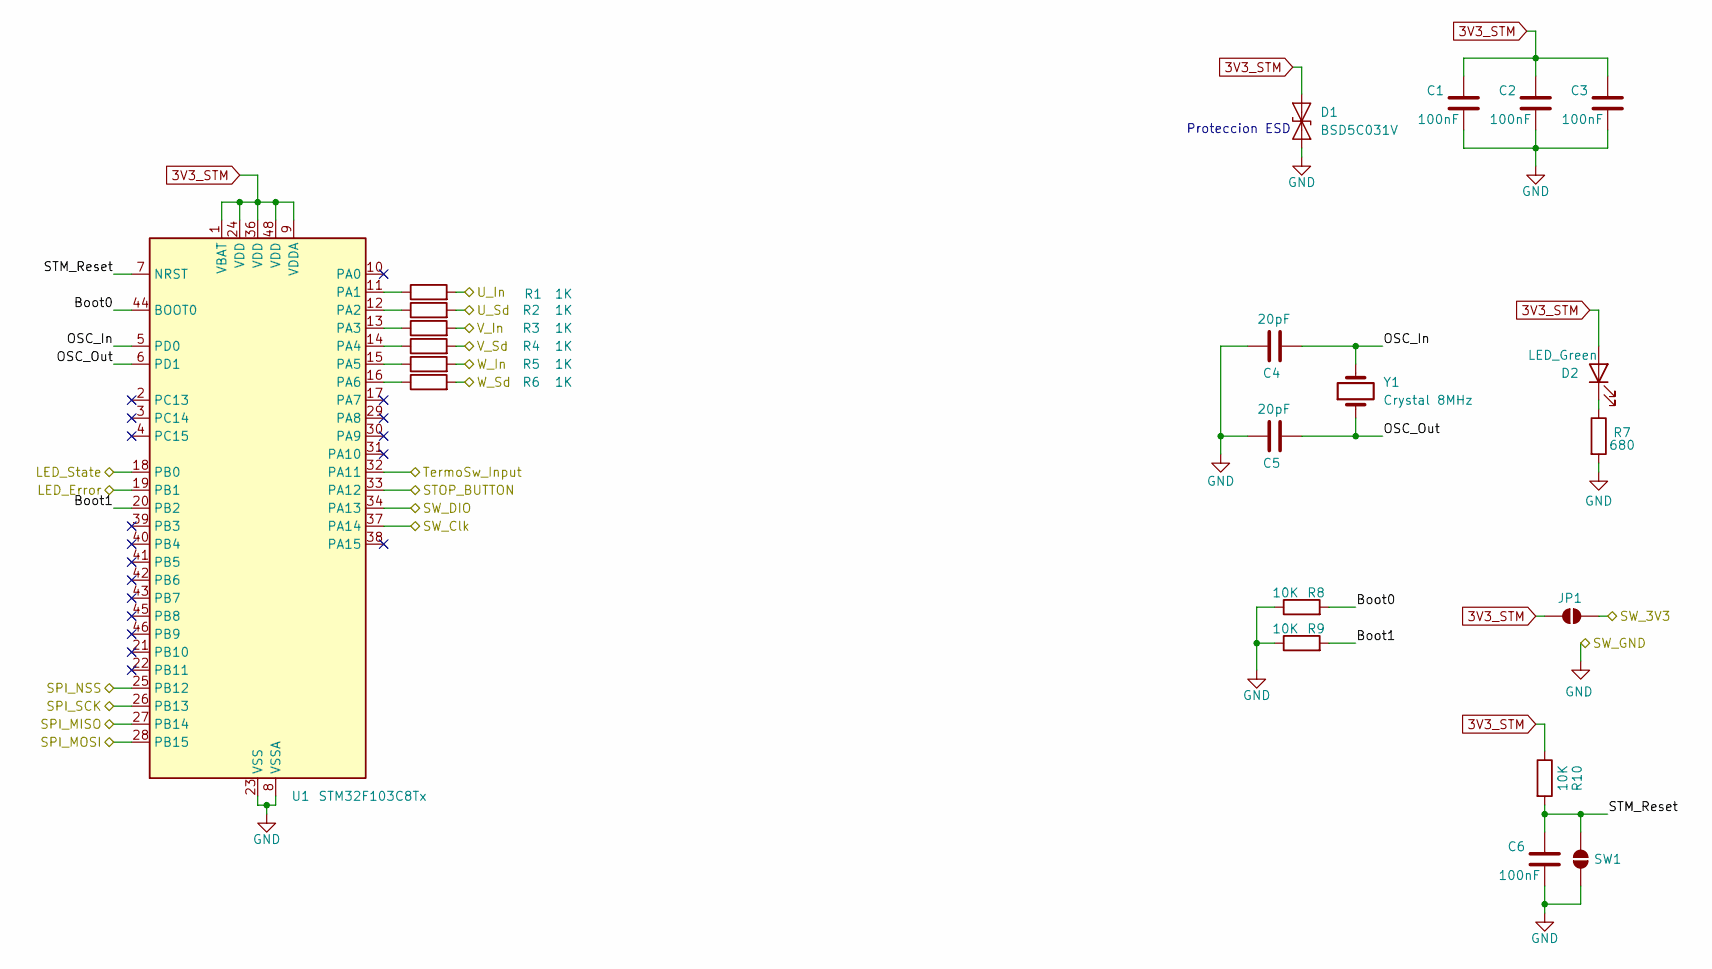
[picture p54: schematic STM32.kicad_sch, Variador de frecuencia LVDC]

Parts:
C1, C2, C3, C6: 100nF; C_0603_1608Metric_Pad1.08x0.95mm_HandSolder
C4, C5: 20pF; C_0603_1608Metric_Pad1.08x0.95mm_HandSolder
D1: BSD5C031V; D_SOD-523
D2: LED_Green; LED_0603_1608Metric_Pad1.05x0.95mm_HandSolder
JP1: SolderJumper_2_Open; SolderJumper-2_P1.3mm_Open_RoundedPad1.0x1.5mm
R1, R2, R3, R4, R5, R6: 1K; R_0603_1608Metric_Pad0.98x0.95mm_HandSolder
R7: 680; R_0603_1608Metric_Pad0.98x0.95mm_HandSolder
R8, R9, R10: 10K; R_0603_1608Metric_Pad0.98x0.95mm_HandSolder
SW1: SolderJumper_2_Open; SolderJumper-2_P1.3mm_Open_RoundedPad1.0x1.5mm
U1: STM32F103C8Tx; LQFP-48_7x7mm_P0.5mm
Y1: Crystal 8MHz; Crystal_SMD_5032-2Pin_5.0x3.2mm

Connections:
3V3_STM: C1.1, C2.1, C3.1, D1.2 (A2), D2.2 (A), JP1.1 (A), R10.1, U1.1 (VBAT), U1.9 (VDDA), U1.24 (VDD), U1.36 (VDD), U1.48 (VDD); also elsewhere on the board
/ESP32/MISO: U1.27 (PB14); also elsewhere on the board
/ESP32/MOSI: U1.28 (PB15); also elsewhere on the board
/ESP32/NSS: U1.25 (PB12); also elsewhere on the board
/ESP32/SCK: U1.26 (PB13); also elsewhere on the board
/Perifericos/LED_Error: U1.19 (PB1); also elsewhere on the board
/Perifericos/LED_State: U1.18 (PB0); also elsewhere on the board
/Perifericos/TermoSw_Input: U1.32 (PA11); also elsewhere on the board
/STM32/Boot0: R8.2, U1.44 (BOOT0)
/STM32/Boot1: R9.2, U1.20 (PB2)
/STM32/OSC_In: C4.1, U1.5 (PD0), Y1.2
/STM32/OSC_Out: C5.1, U1.6 (PD1), Y1.1
/STM32/STM_Reset: C6.1, R10.2, SW1.2 (B), U1.7 (NRST)
/STM32/STOP_BUTTON: U1.33 (PA12)
/STM32/SW_3V3: JP1.2 (B); also elsewhere on the board
/STM32/SW_Clk: U1.37 (PA14); also elsewhere on the board
/STM32/SW_DIO: U1.34 (PA13); also elsewhere on the board
/STM32/U_In: R1.2; also elsewhere on the board
/STM32/U_Sd: R2.2; also elsewhere on the board
/STM32/V_In: R3.2; also elsewhere on the board
/STM32/V_Sd: R4.2; also elsewhere on the board
/STM32/W_In: R5.2; also elsewhere on the board
/STM32/W_Sd: R6.2; also elsewhere on the board
GND: C1.2, C2.2, C3.2, C4.2, C5.2, C6.2, D1.1 (A1), R7.2, R8.1, R9.1, SW1.1 (A), U1.8 (VSSA), U1.23 (VSS), U1.35 (VSS), U1.47 (VSS); also elsewhere on the board
unnamed: D2.1 (K), R7.1
unnamed: R1.1, U1.11 (PA1)
unnamed: R2.1, U1.12 (PA2)
unnamed: R3.1, U1.13 (PA3)
unnamed: R4.1, U1.14 (PA4)
unnamed: R5.1, U1.15 (PA5)
unnamed: R6.1, U1.16 (PA6)

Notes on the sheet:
Proteccion ESD

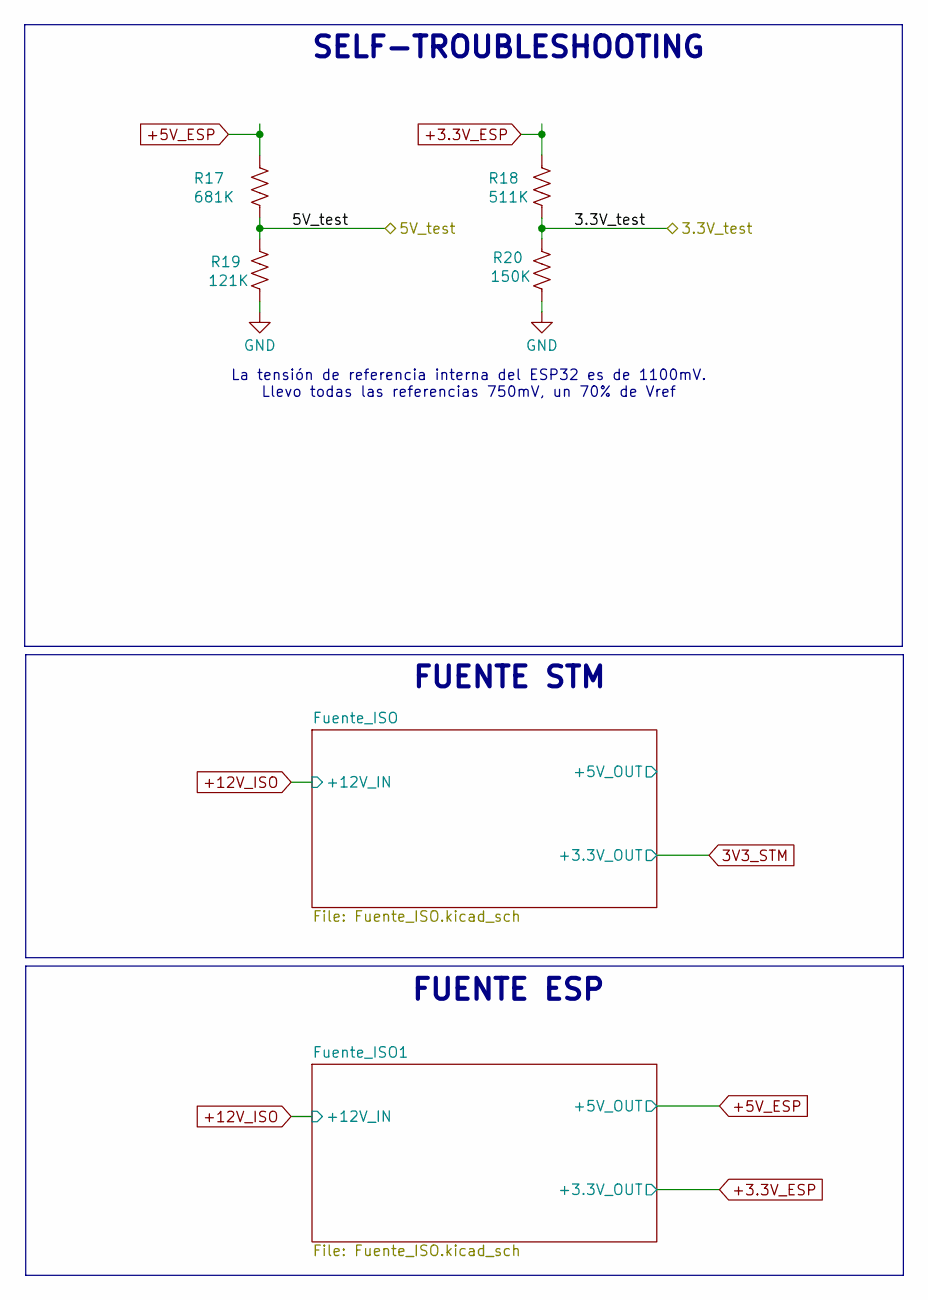
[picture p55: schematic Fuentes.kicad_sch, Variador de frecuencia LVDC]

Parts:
R17: 681K; R_0603_1608Metric_Pad0.98x0.95mm_HandSolder
R18: 511K; R_0603_1608Metric_Pad0.98x0.95mm_HandSolder
R19: 121K; R_0603_1608Metric_Pad0.98x0.95mm_HandSolder
R20: 150K; R_0603_1608Metric_Pad0.98x0.95mm_HandSolder

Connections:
+3.3V_ESP: R18.1; also elsewhere on the board
+5V_ESP: R17.1; also elsewhere on the board
/ESP32/3.3V_test: R18.2, R20.1; also elsewhere on the board
/ESP32/5V_test: R17.2, R19.1; also elsewhere on the board
GND: R19.2, R20.2; also elsewhere on the board

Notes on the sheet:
FUENTE ESP
FUENTE STM
SELF-TROUBLESHOOTING
La tensión de referencia interna del ESP32 es de 1100mV. Llevo todas las referencias 750mV, un 70% de Vref

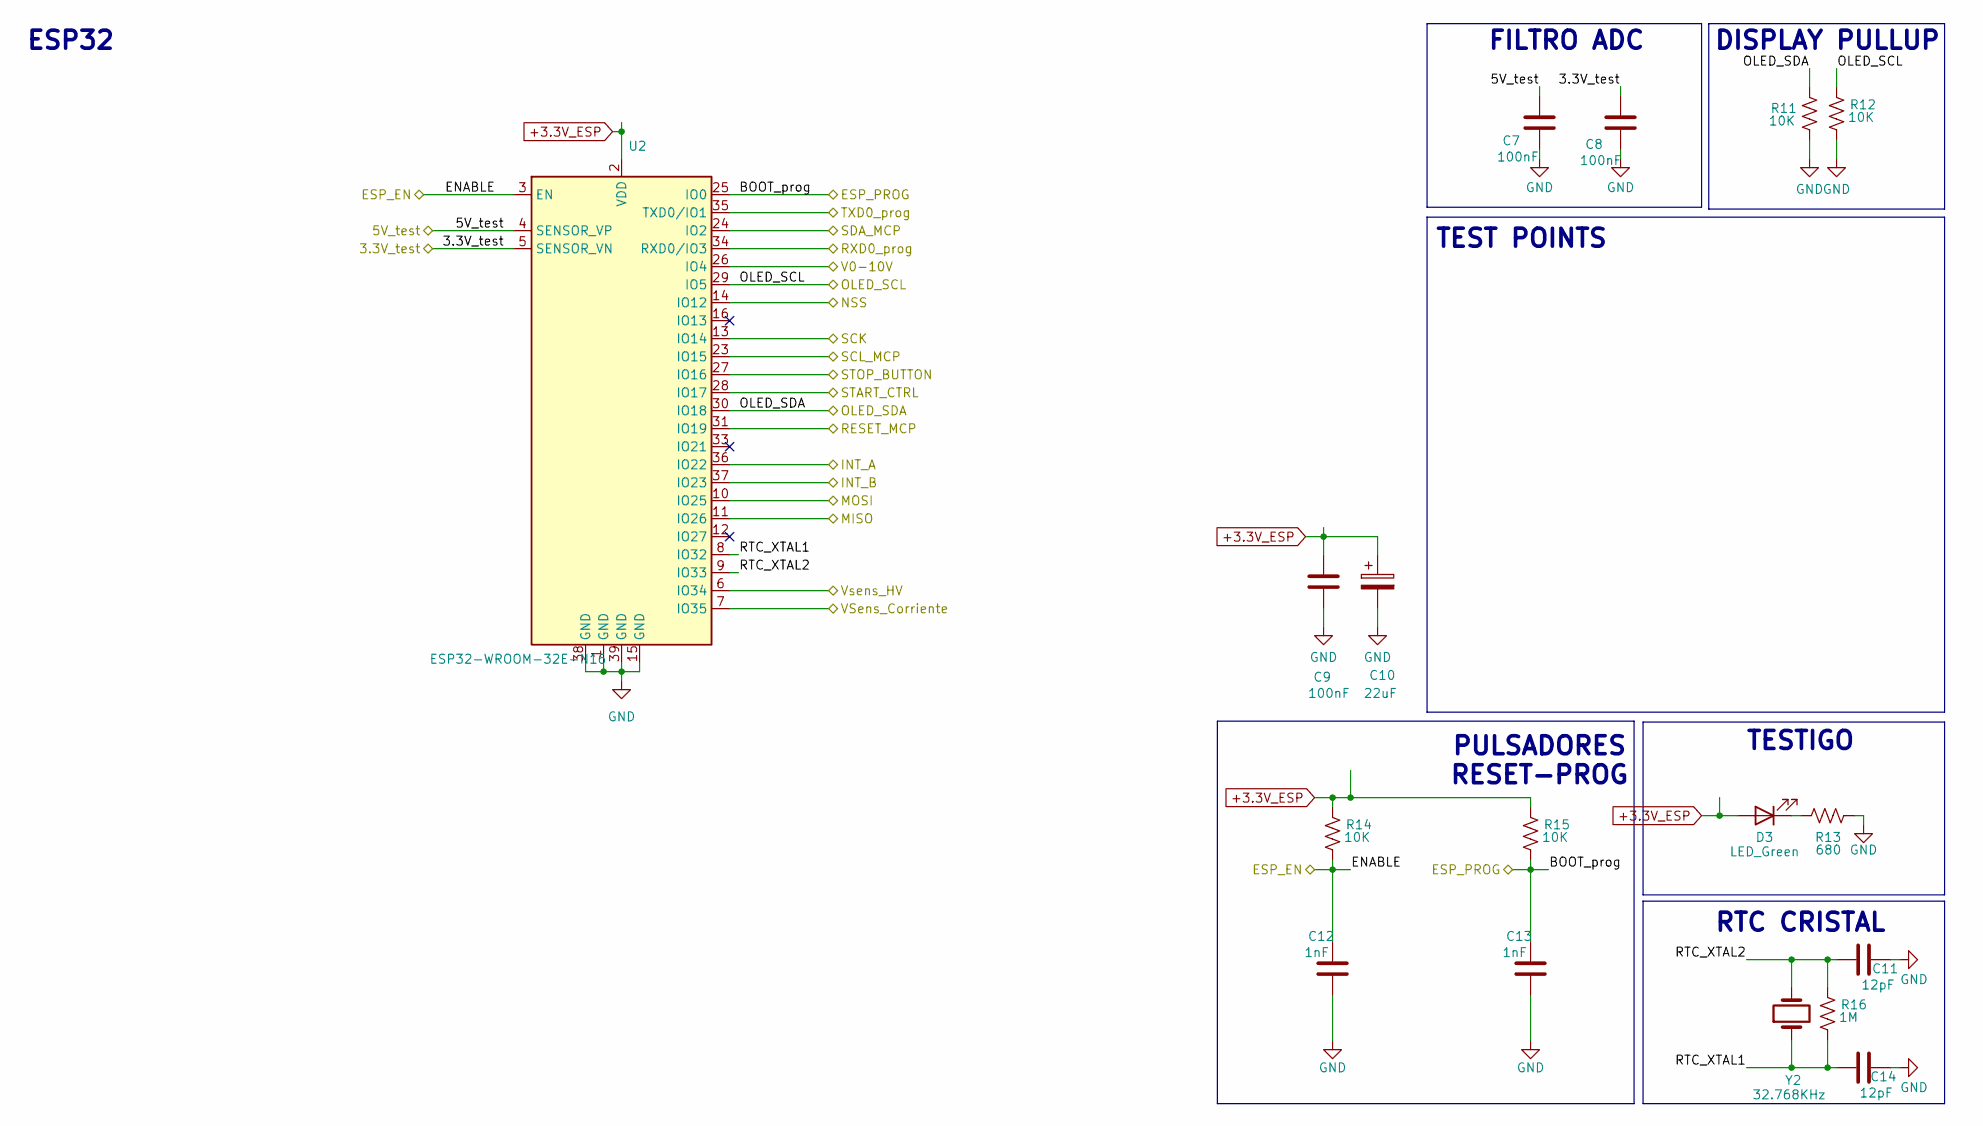
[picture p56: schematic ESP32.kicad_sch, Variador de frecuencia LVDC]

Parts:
C7, C8, C9: 100nF; C_0603_1608Metric_Pad1.08x0.95mm_HandSolder
C10: 22uF; CP_Elec_5x5.4
C11, C14: 12pF; C_0603_1608Metric
C12, C13: 1nF; C_0603_1608Metric
D3: LED_Green; LED_0603_1608Metric_Pad1.05x0.95mm_HandSolder
R11, R12, R14, R15: 10K; R_0603_1608Metric_Pad0.98x0.95mm_HandSolder
R13: 680; R_0603_1608Metric_Pad0.98x0.95mm_HandSolder
R16: 1M; R_0603_1608Metric_Pad0.98x0.95mm_HandSolder
U2: ESP32-WROOM-32E-N16; ESP32-WROOM-32E
Y2: 32.768KHz; Crystal_SMD_3215-2Pin_3.2x1.5mm

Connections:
+3.3V_ESP: C9.1, C10.1, D3.2 (A), R14.1, R15.1, U2.2 (VDD); also elsewhere on the board
/ESP32/3.3V_test: C8.1, U2.5 (SENSOR_VN); also elsewhere on the board
/ESP32/5V_test: C7.1, U2.4 (SENSOR_VP); also elsewhere on the board
/ESP32/BOOT_prog: C13.1, R15.2, U2.25 (IO0); also elsewhere on the board
/ESP32/ENABLE: C12.1, R14.2, U2.3 (EN); also elsewhere on the board
/ESP32/INT_A: U2.36 (IO22); also elsewhere on the board
/ESP32/INT_B: U2.37 (IO23); also elsewhere on the board
/ESP32/MISO: U2.11 (IO26); also elsewhere on the board
/ESP32/MOSI: U2.10 (IO25); also elsewhere on the board
/ESP32/NSS: U2.14 (IO12); also elsewhere on the board
/ESP32/OLED_SCL: R12.1, U2.29 (IO5); also elsewhere on the board
/ESP32/OLED_SDA: R11.1, U2.30 (IO18); also elsewhere on the board
/ESP32/RESET_MCP: U2.31 (IO19); also elsewhere on the board
/ESP32/RTC_XTAL1: C14.2, R16.2, U2.8 (IO32), Y2.1
/ESP32/RTC_XTAL2: C11.1, R16.1, U2.9 (IO33), Y2.2
/ESP32/RXD0_prog: U2.34 (RXD0/IO3); also elsewhere on the board
/ESP32/SCK: U2.13 (IO14); also elsewhere on the board
/ESP32/SCL_MCP: U2.23 (IO15); also elsewhere on the board
/ESP32/SDA_MCP: U2.24 (IO2); also elsewhere on the board
/ESP32/START_CTRL: U2.28 (IO17); also elsewhere on the board
/ESP32/STOP_BUTTON: U2.27 (IO16); also elsewhere on the board
/ESP32/TXD0_prog: U2.35 (TXD0/IO1); also elsewhere on the board
/ESP32/V0-10V: U2.26 (IO4); also elsewhere on the board
/ESP32/VSens_Corriente: U2.7 (IO35); also elsewhere on the board
/ESP32/Vsens_HV: U2.6 (IO34); also elsewhere on the board
GND: C7.2, C8.2, C9.2, C10.2, C11.2, C12.2, C13.2, C14.1, R11.2, R12.2, R13.2, U2.1 (GND), U2.15 (GND), U2.38 (GND), U2.39 (GND); also elsewhere on the board
unnamed: D3.1 (K), R13.1

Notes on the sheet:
DISPLAY PULLUP
ESP32
FILTRO ADC
TESTIGO
PULSADORES RESET-PROG
TEST POINTS
RTC CRISTAL

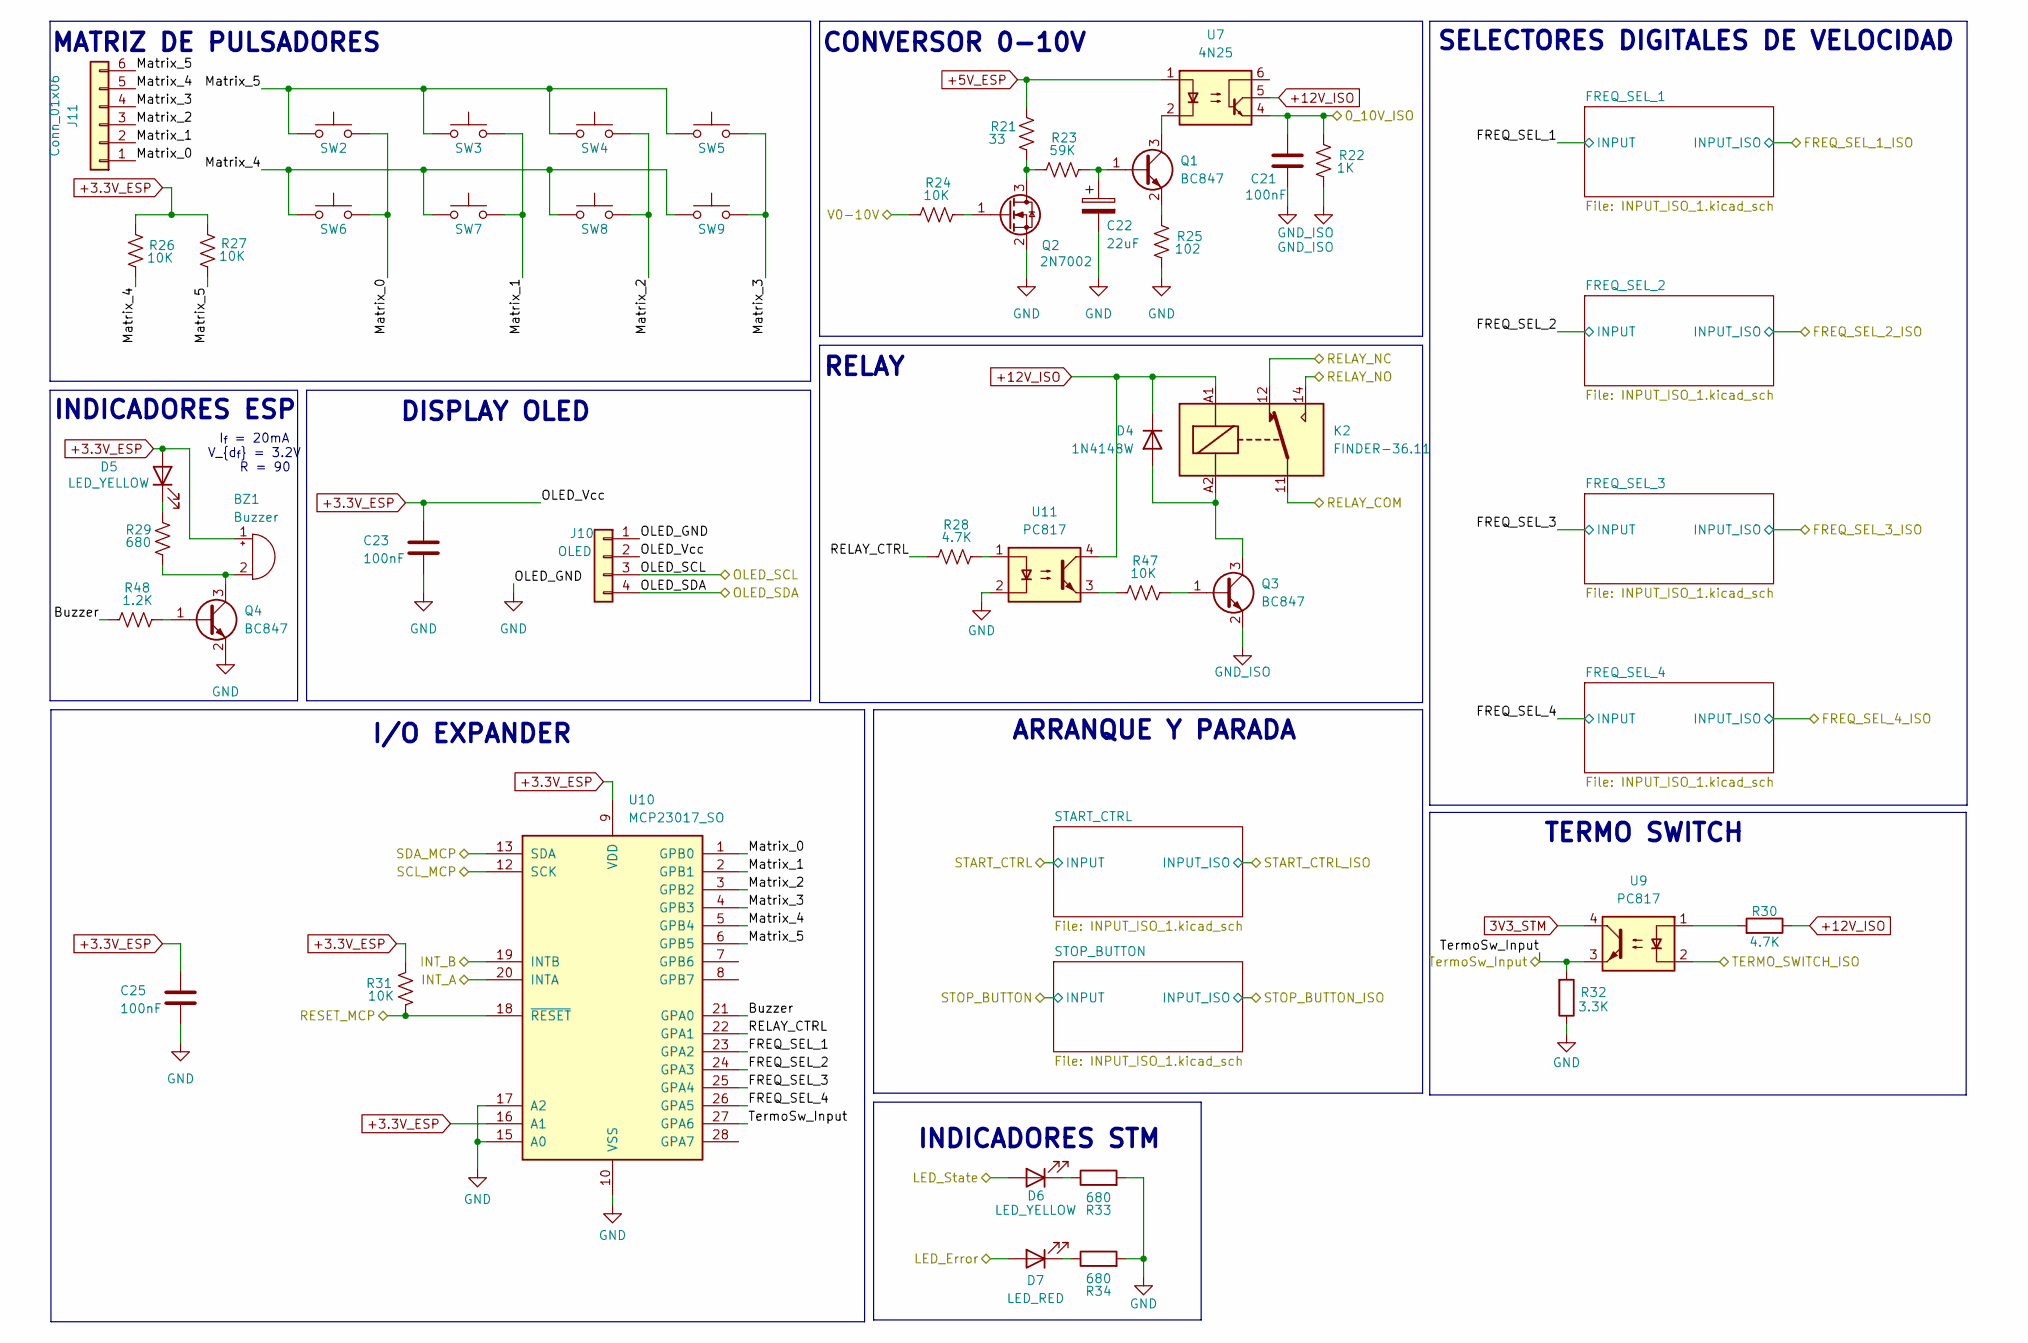
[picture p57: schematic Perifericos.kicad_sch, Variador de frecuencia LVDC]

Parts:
BZ1: Buzzer; Buzzer_12x9.5RM7.6
C21, C23, C25: 100nF; C_0603_1608Metric_Pad1.08x0.95mm_HandSolder
C22: 22uF; CP_Elec_5x5.4
D4: 1N4148W; D_SOD-123
D5, D6: LED_YELLOW; LED_0603_1608Metric_Pad1.05x0.95mm_HandSolder
D7: LED_RED; LED_0603_1608Metric_Pad1.05x0.95mm_HandSolder
J10: OLED; PinHeader_1x04_P2.54mm_Horizontal
J11: Conn_01x06; PinHeader_1x06_P2.54mm_Horizontal
K2: FINDER-36.11; Relay_SPDT_Finder_36.11
Q1, Q3, Q4: BC847; SOT-523
Q2: 2N7002; SOT-23
R21: 33; R_1210_3225Metric_Pad1.30x2.65mm_HandSolder
R22: 1K; R_0603_1608Metric_Pad0.98x0.95mm_HandSolder
R23: 59K; R_0603_1608Metric_Pad0.98x0.95mm_HandSolder
R24, R26, R27, R31, R47: 10K; R_0603_1608Metric_Pad0.98x0.95mm_HandSolder
R25: 102; R_0603_1608Metric_Pad0.98x0.95mm_HandSolder
R28, R30: 4.7K; R_0603_1608Metric_Pad0.98x0.95mm_HandSolder
R29, R33, R34: 680; R_0603_1608Metric_Pad0.98x0.95mm_HandSolder
R32: 3.3K; R_0603_1608Metric_Pad0.98x0.95mm_HandSolder
R48: 1.2K; R_0603_1608Metric_Pad0.98x0.95mm_HandSolder
SW2, SW3, SW4, SW5, SW6, SW7, SW8, SW9: SW_MEC_5G; SW_Push_SPST_NO_Alps_SKRK
U7: 4N25; DIP-6_W7.62mm_SMDSocket_SmallPads
U9, U11: PC817; DIP-4_W7.62mm_SMDSocket_SmallPads
U10: MCP23017_SO; SOIC-28W_7.5x17.9mm_P1.27mm

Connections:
3V3_STM: U9.4; also elsewhere on the board
+3.3V_ESP: BZ1.1 (+), C23.1, C25.1, D5.2 (A), J10.2, R26.1, R27.1, R31.1, U10.9 (VDD), U10.16 (A1); also elsewhere on the board
+5V_ESP: R21.2, U7.1; also elsewhere on the board
+12V_ISO: D4.1 (K), K2.A1, R30.1, U7.5, U11.4; also elsewhere on the board
/ESP32/INT_A: U10.20 (INTA); also elsewhere on the board
/ESP32/INT_B: U10.19 (INTB); also elsewhere on the board
/ESP32/OLED_SCL: J10.3; also elsewhere on the board
/ESP32/OLED_SDA: J10.4; also elsewhere on the board
/ESP32/RESET_MCP: R31.2, U10.18 (~RESET); also elsewhere on the board
/ESP32/SCL_MCP: U10.12 (SCK); also elsewhere on the board
/ESP32/SDA_MCP: U10.13 (SDA); also elsewhere on the board
/ESP32/V0-10V: R24.1; also elsewhere on the board
/Perifericos/0_10V_ISO: C21.1, R22.2, U7.4; also elsewhere on the board
/Perifericos/Buzzer: R48.1, U10.21 (GPA0)
/Perifericos/FREQ_SEL_1: U10.23 (GPA2); also elsewhere on the board
/Perifericos/FREQ_SEL_2: U10.24 (GPA3); also elsewhere on the board
/Perifericos/FREQ_SEL_3: U10.25 (GPA4); also elsewhere on the board
/Perifericos/FREQ_SEL_4: U10.26 (GPA5); also elsewhere on the board
/Perifericos/LED_Error: D7.2 (A); also elsewhere on the board
/Perifericos/LED_State: D6.2 (A); also elsewhere on the board
/Perifericos/Matrix_0: J11.1, SW2.2 (B), SW6.2 (B), U10.1 (GPB0)
/Perifericos/Matrix_1: J11.2, SW3.2 (B), SW7.2 (B), U10.2 (GPB1)
/Perifericos/Matrix_2: J11.3, SW4.2 (B), SW8.2 (B), U10.3 (GPB2)
/Perifericos/Matrix_3: J11.4, SW5.2 (B), SW9.2 (B), U10.4 (GPB3)
/Perifericos/Matrix_4: J11.5, R26.2, SW6.1 (A), SW7.1 (A), SW8.1 (A), SW9.1 (A), U10.5 (GPB4)
/Perifericos/Matrix_5: J11.6, R27.2, SW2.1 (A), SW3.1 (A), SW4.1 (A), SW5.1 (A), U10.6 (GPB5)
/Perifericos/RELAY_COM: K2.11; also elsewhere on the board
/Perifericos/RELAY_CTRL: R28.1, U10.22 (GPA1)
/Perifericos/RELAY_NC: K2.12; also elsewhere on the board
/Perifericos/RELAY_NO: K2.14; also elsewhere on the board
/Perifericos/TERMO_SWITCH_ISO: U9.2; also elsewhere on the board
/Perifericos/TermoSw_Input: R32.2, U9.3, U10.27 (GPA6); also elsewhere on the board
GND: C22.2, C23.2, C25.2, J10.1, Q2.2 (S), Q4.2 (E), R25.1, R32.1, R33.2, R34.2, U10.10 (VSS), U10.15 (A0), U10.17 (A2), U11.2; also elsewhere on the board
GND_ISO: C21.2, Q3.2 (E), R22.1; also elsewhere on the board
unnamed: BZ1.2 (-), Q4.3 (C), R29.2
unnamed: D4.2 (A), K2.A2, Q3.3 (C)
unnamed: D5.1 (K), R29.1
unnamed: D6.1 (K), R33.1
unnamed: D7.1 (K), R34.1
unnamed: C22.1, Q1.1 (B), R23.2
unnamed: Q1.3 (C), U7.2
unnamed: Q1.2 (E), R25.2
unnamed: Q2.3 (D), R21.1, R23.1
unnamed: Q2.1 (G), R24.2
unnamed: Q3.1 (B), R47.2
unnamed: Q4.1 (B), R48.2
unnamed: R28.2, U11.1
unnamed: R30.2, U9.1
unnamed: R47.1, U11.3

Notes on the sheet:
R = 90
I_{f} = 20mA V_{d_{f}} = 3.2V
RELAY
MATRIZ DE PULSADORES
ARRANQUE Y PARADA
INDICADORES STM
TERMO SWITCH
I/O EXPANDER
DISPLAY OLED
INDICADORES ESP
SELECTORES DIGITALES DE VELOCIDAD
CONVERSOR 0-10V

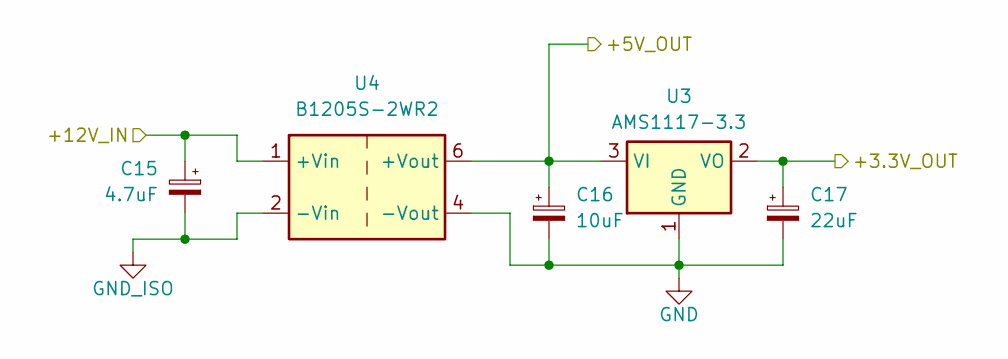
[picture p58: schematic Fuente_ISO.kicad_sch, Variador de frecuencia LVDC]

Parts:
C15: 4.7uF; C_0603_1608Metric
C16: 10uF; CP_Elec_4x5.4
C17: 22uF; CP_Elec_4x5.4
U3: AMS1117-3.3; SOT-223-3_TabPin2
U4: B1205S-2WR2; Converter_DCDC_TRACO_TMA-05xxS_12xxS_Single_THT

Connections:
3V3_STM: C17.1, U3.2 (VO); also elsewhere on the board
+12V_ISO: C15.1, U4.1 (+Vin); also elsewhere on the board
/Fuentes/Fuente_ISO/+5V_OUT: C16.1, U3.3 (VI), U4.6 (+Vout)
GND: C16.2, C17.2, U3.1 (GND), U4.4 (-Vout); also elsewhere on the board
GND_ISO: C15.2, U4.2 (-Vin); also elsewhere on the board

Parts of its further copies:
C18: 4.7uF; C_0603_1608Metric
C19: 10uF; CP_Elec_4x5.4
C20: 22uF; CP_Elec_4x5.4
U5: AMS1117-3.3; SOT-223-3_TabPin2
U6: B1205S-2WR2; Converter_DCDC_TRACO_TMA-05xxS_12xxS_Single_THT

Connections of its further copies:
+3.3V_ESP: C20.1, U5.2 (VO); also elsewhere on the board
+5V_ESP: C19.1, U5.3 (VI), U6.6 (+Vout); also elsewhere on the board
+12V_ISO: C18.1, U6.1 (+Vin); also elsewhere on the board
GND: C19.2, C20.2, U5.1 (GND), U6.4 (-Vout); also elsewhere on the board
GND_ISO: C18.2, U6.2 (-Vin); also elsewhere on the board

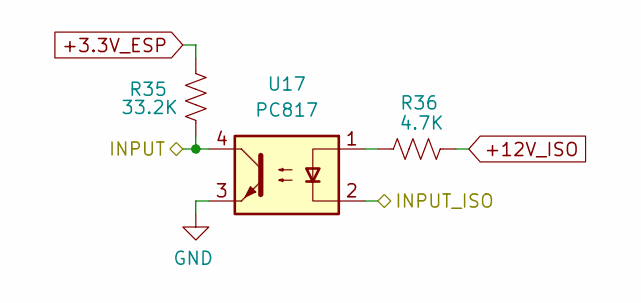
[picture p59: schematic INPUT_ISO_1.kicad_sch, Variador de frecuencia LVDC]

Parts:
R35: 33.2K; R_0603_1608Metric_Pad0.98x0.95mm_HandSolder
R36: 4.7K; R_0603_1608Metric_Pad0.98x0.95mm_HandSolder
U17: PC817; DIP-4_W7.62mm_SMDSocket_SmallPads

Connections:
+3.3V_ESP: R35.2; also elsewhere on the board
+12V_ISO: R36.2; also elsewhere on the board
/Perifericos/FREQ_SEL_1: R35.1, U17.4; also elsewhere on the board
/Perifericos/FREQ_SEL_1_ISO: U17.2; also elsewhere on the board
GND: U17.3; also elsewhere on the board
unnamed: R36.1, U17.1

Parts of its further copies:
R37, R39, R41, R43, R45: 33.2K; R_0603_1608Metric_Pad0.98x0.95mm_HandSolder
R38, R40, R42, R44, R46: 4.7K; R_0603_1608Metric_Pad0.98x0.95mm_HandSolder
U18, U19, U20, U21, U22: PC817; DIP-4_W7.62mm_SMDSocket_SmallPads

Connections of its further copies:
+3.3V_ESP: R37.2, R39.2, R41.2, R43.2, R45.2; also elsewhere on the board
+12V_ISO: R38.2, R40.2, R42.2, R44.2, R46.2; also elsewhere on the board
/ESP32/START_CTRL: R43.1, U21.4; also elsewhere on the board
/ESP32/STOP_BUTTON: R45.1, U22.4; also elsewhere on the board
/Perifericos/FREQ_SEL_2: R37.1, U18.4; also elsewhere on the board
/Perifericos/FREQ_SEL_2_ISO: U18.2; also elsewhere on the board
/Perifericos/FREQ_SEL_3: R39.1, U19.4; also elsewhere on the board
/Perifericos/FREQ_SEL_3_ISO: U19.2; also elsewhere on the board
/Perifericos/FREQ_SEL_4: R41.1, U20.4; also elsewhere on the board
/Perifericos/FREQ_SEL_4_ISO: U20.2; also elsewhere on the board
/Perifericos/START_CTRL_ISO: U21.2; also elsewhere on the board
/Perifericos/STOP_BUTTON_ISO: U22.2; also elsewhere on the board
GND: U18.3, U19.3, U20.3, U21.3, U22.3; also elsewhere on the board
unnamed: R38.1, U18.1
unnamed: R40.1, U19.1
unnamed: R42.1, U20.1
unnamed: R44.1, U21.1
unnamed: R46.1, U22.1

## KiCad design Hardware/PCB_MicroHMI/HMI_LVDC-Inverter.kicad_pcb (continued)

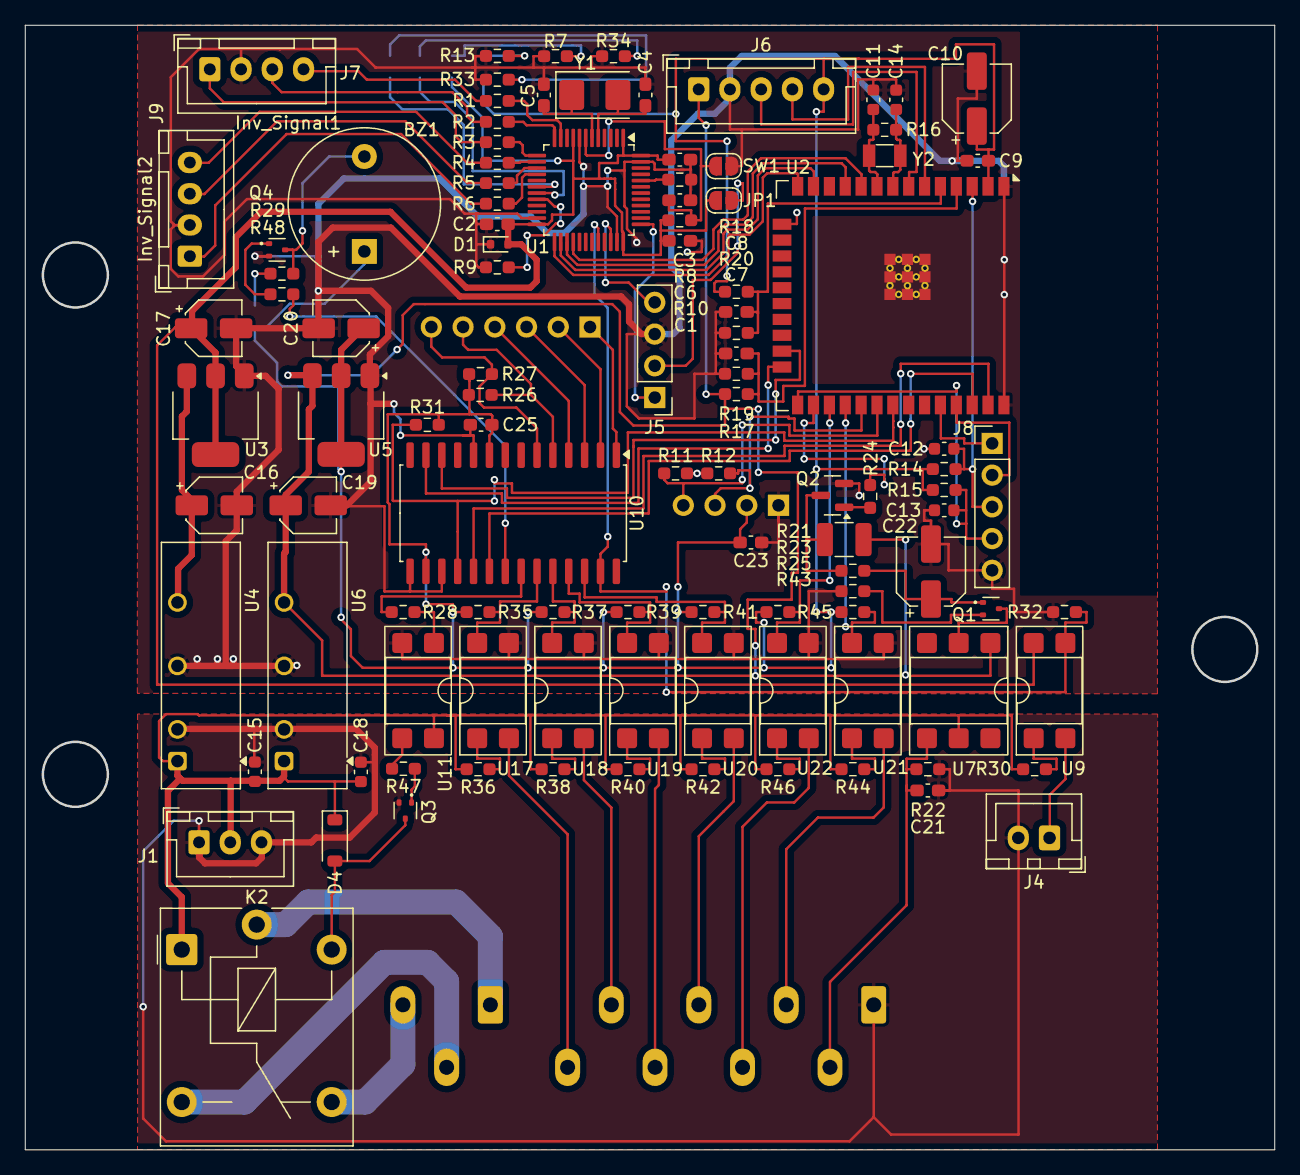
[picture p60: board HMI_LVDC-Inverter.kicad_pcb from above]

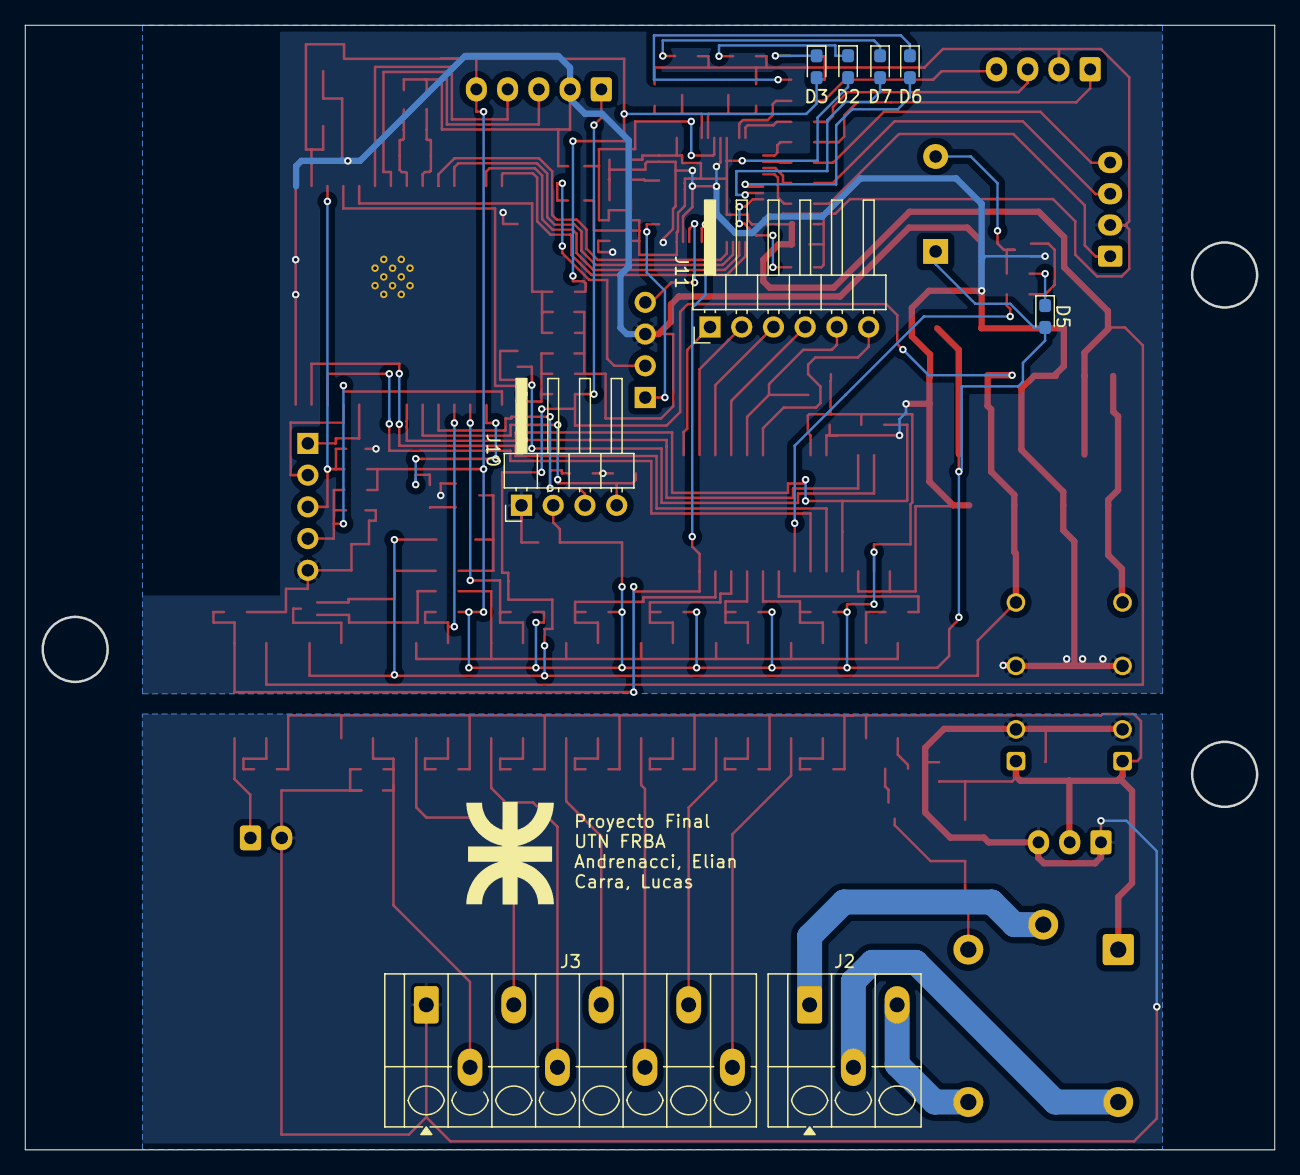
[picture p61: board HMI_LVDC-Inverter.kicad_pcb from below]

Board: 2 copper layers, 100.0 x 90.0 mm, 116 parts (9 on the bottom side), 100 nets.

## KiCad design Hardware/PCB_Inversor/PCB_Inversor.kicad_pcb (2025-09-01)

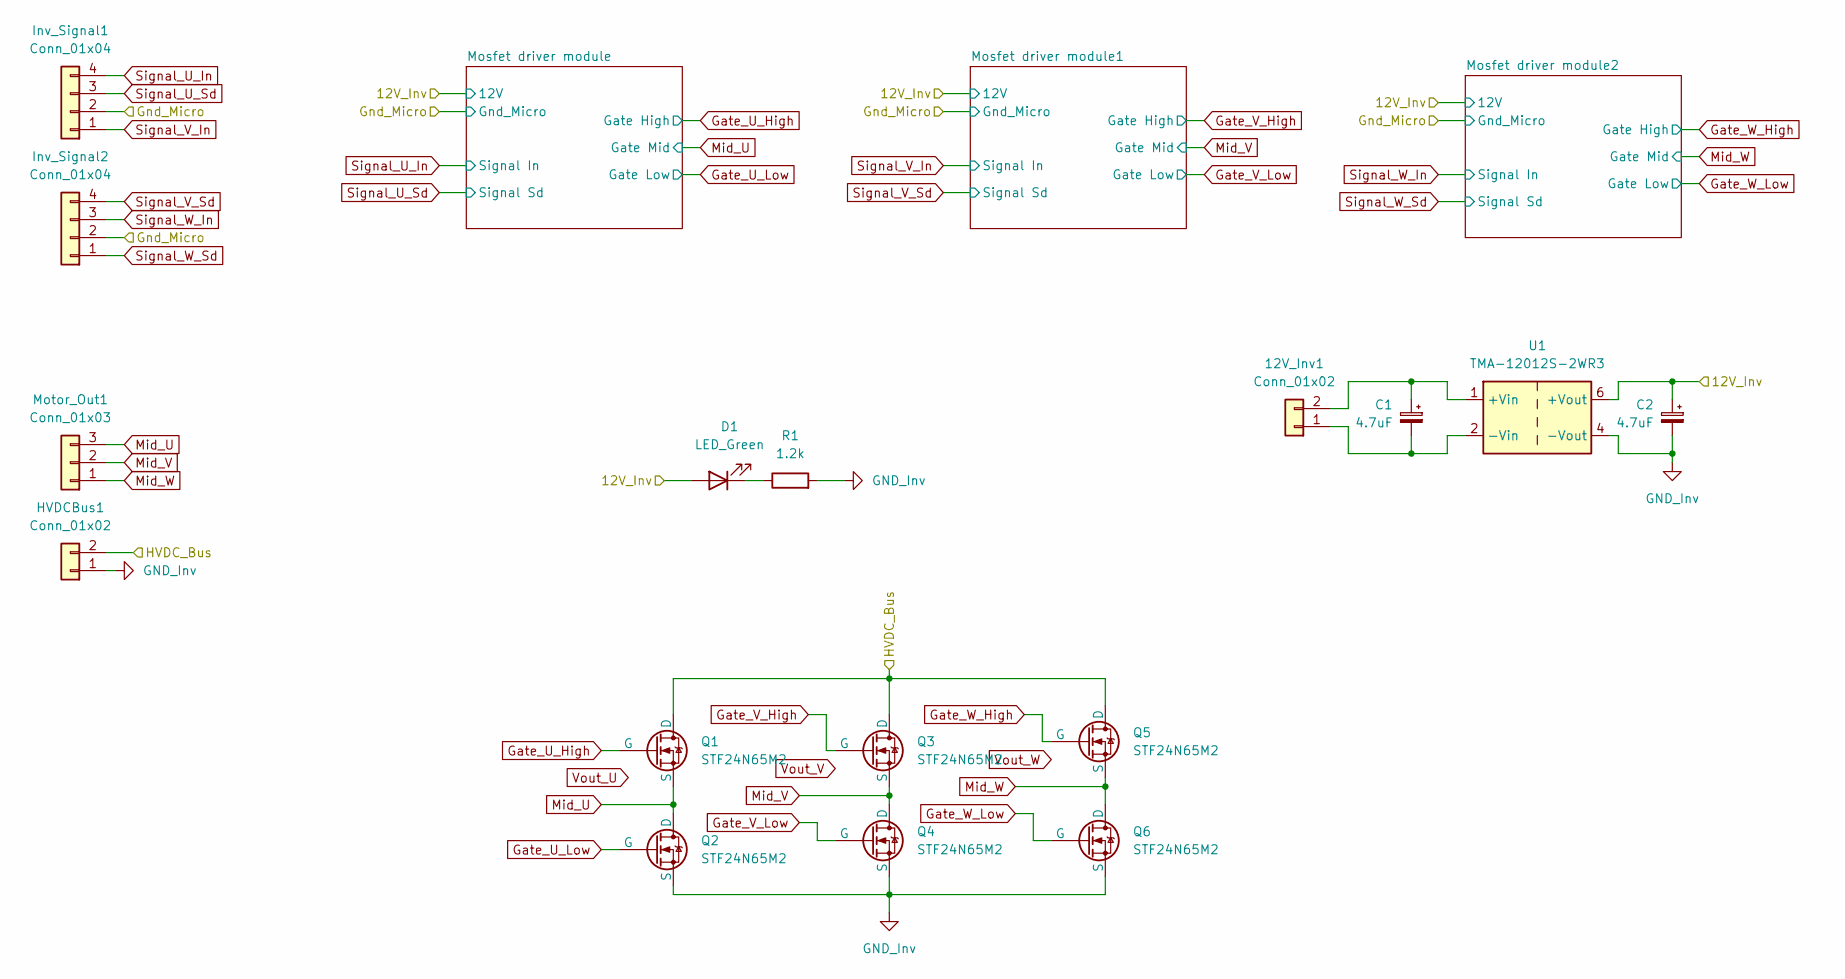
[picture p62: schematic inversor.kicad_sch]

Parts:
12V_Inv1: Conn_01x02; JST_XH_B2B-XH-A_1x02_P2.50mm_Vertical
C1, C2: 4.7uF; CP_Elec_4x5.4
D1: LED_Green; LED_0603_1608Metric_Pad1.05x0.95mm_HandSolder
HVDCBus1: Conn_01x02; PhoenixContact_MSTBVA_2,5_2-G-5,08_1x02_P5.08mm_Vertical
Inv_Signal1, Inv_Signal2: Conn_01x04; JST_XH_B4B-XH-A_1x04_P2.50mm_Vertical
Motor_Out1: Conn_01x03; PhoenixContact_MCV_1,5_3-G-5.08_1x03_P5.08mm_Vertical
Q1, Q2, Q3, Q4, Q5, Q6: STF24N65M2; TO-220-3_Horizontal_TabUp
R1: 1.2k; R_0603_1608Metric_Pad0.98x0.95mm_HandSolder
U1: TMA-12012S-2WR3; Converter_DCDC_TRACO_TMA-05xxS_12xxS_Single_THT

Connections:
/Inversor/12V_Inv: C2.1, D1.2 (A), U1.6 (+Vout); also elsewhere on the board
/Inversor/Gnd_Micro: Inv_Signal1.2, Inv_Signal2.2; also elsewhere on the board
/Inversor/HVDC_Bus: HVDCBus1.2, Q1.2 (D), Q3.2 (D), Q5.2 (D)
GND_Inv: C2.2, HVDCBus1.1, Q2.3 (S), Q4.3 (S), Q6.3 (S), R1.2, U1.4 (-Vout); also elsewhere on the board
Gate_U_High: Q1.1 (G); also elsewhere on the board
Gate_U_Low: Q2.1 (G); also elsewhere on the board
Gate_V_High: Q3.1 (G); also elsewhere on the board
Gate_V_Low: Q4.1 (G); also elsewhere on the board
Gate_W_High: Q5.1 (G); also elsewhere on the board
Gate_W_Low: Q6.1 (G); also elsewhere on the board
Mid_U: Motor_Out1.3, Q1.3 (S), Q2.2 (D); also elsewhere on the board
Mid_V: Motor_Out1.2, Q3.3 (S), Q4.2 (D); also elsewhere on the board
Mid_W: Motor_Out1.1, Q5.3 (S), Q6.2 (D); also elsewhere on the board
unnamed: 12V_Inv1.1, C1.2, U1.2 (-Vin)
unnamed: 12V_Inv1.2, C1.1, U1.1 (+Vin)
unnamed: D1.1 (K), R1.1
Signal_U_In: Inv_Signal1.4; also elsewhere on the board
Signal_U_Sd: Inv_Signal1.3; also elsewhere on the board
Signal_V_In: Inv_Signal1.1; also elsewhere on the board
Signal_V_Sd: Inv_Signal2.4; also elsewhere on the board
Signal_W_In: Inv_Signal2.3; also elsewhere on the board
Signal_W_Sd: Inv_Signal2.1; also elsewhere on the board

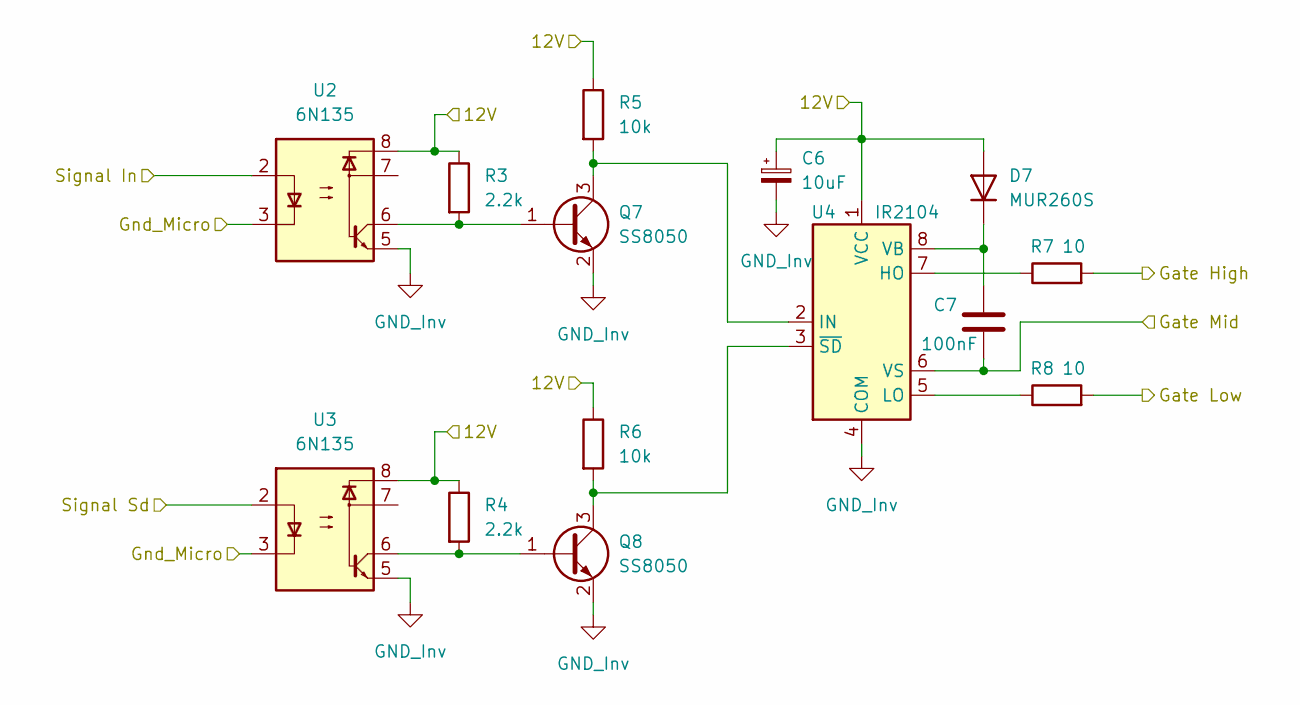
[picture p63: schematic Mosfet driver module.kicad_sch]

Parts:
C6: 10uF; CP_Elec_4x5.4
C7: 100nF; C_0603_1608Metric_Pad1.08x0.95mm_HandSolder
D7: MUR260S; D_SOD-523
Q7, Q8: SS8050; SOT-23
R3, R4: 2.2k; R_0603_1608Metric_Pad0.98x0.95mm_HandSolder
R5, R6: 10k; R_0603_1608Metric_Pad0.98x0.95mm_HandSolder
R7, R8: 10; R_0603_1608Metric_Pad0.98x0.95mm_HandSolder
U2, U3: 6N135; SOP-8_6.62x9.15mm_P2.54mm
U4: IR2104; SOIC-8_3.9x4.9mm_P1.27mm

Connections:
/Inversor/12V_Inv: C6.1, D7.2 (A), R3.1, R4.1, R5.1, R6.1, U2.8, U3.8, U4.1 (VCC); also elsewhere on the board
/Inversor/Gnd_Micro: U2.3, U3.3; also elsewhere on the board
GND_Inv: C6.2, Q7.2 (E), Q8.2 (E), U2.5, U3.5, U4.4 (COM); also elsewhere on the board
Gate_U_High: R7.2; also elsewhere on the board
Gate_U_Low: R8.2; also elsewhere on the board
Mid_U: C7.2, U4.6 (VS); also elsewhere on the board
unnamed: C7.1, D7.1 (K), U4.8 (VB)
unnamed: Q7.1 (B), R3.2, U2.6
unnamed: Q7.3 (C), R5.2, U4.2 (IN)
unnamed: Q8.1 (B), R4.2, U3.6
unnamed: Q8.3 (C), R6.2, U4.3 (~SD)
unnamed: R7.1, U4.7 (HO)
unnamed: R8.1, U4.5 (LO)
Signal_U_In: U2.2; also elsewhere on the board
Signal_U_Sd: U3.2; also elsewhere on the board

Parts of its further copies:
C8, C10: 10uF; CP_Elec_4x5.4
C9, C11: 100nF; C_0603_1608Metric_Pad1.08x0.95mm_HandSolder
D8, D9: MUR260S; D_SOD-523
Q9, Q10, Q11, Q12: SS8050; SOT-23
R9, R10, R15, R16: 2.2k; R_0603_1608Metric_Pad0.98x0.95mm_HandSolder
R11, R12, R17, R18: 10k; R_0603_1608Metric_Pad0.98x0.95mm_HandSolder
R13, R14, R19, R20: 10; R_0603_1608Metric_Pad0.98x0.95mm_HandSolder
U5, U6, U8, U9: 6N135; SOP-8_6.62x9.15mm_P2.54mm
U7, U10: IR2104; SOIC-8_3.9x4.9mm_P1.27mm

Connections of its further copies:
/Inversor/12V_Inv: C8.1, C10.1, D8.2 (A), D9.2 (A), R9.1, R10.1, R11.1, R12.1, R15.1, R16.1, R17.1, R18.1, U5.8, U6.8, U7.1 (VCC), U8.8, U9.8, U10.1 (VCC); also elsewhere on the board
/Inversor/Gnd_Micro: U5.3, U6.3, U8.3, U9.3; also elsewhere on the board
GND_Inv: C8.2, C10.2, Q9.2 (E), Q10.2 (E), Q11.2 (E), Q12.2 (E), U5.5, U6.5, U7.4 (COM), U8.5, U9.5, U10.4 (COM); also elsewhere on the board
Gate_V_High: R13.2; also elsewhere on the board
Gate_V_Low: R14.2; also elsewhere on the board
Gate_W_High: R19.2; also elsewhere on the board
Gate_W_Low: R20.2; also elsewhere on the board
Mid_V: C9.2, U7.6 (VS); also elsewhere on the board
Mid_W: C11.2, U10.6 (VS); also elsewhere on the board
unnamed: C9.1, D8.1 (K), U7.8 (VB)
unnamed: C11.1, D9.1 (K), U10.8 (VB)
unnamed: Q9.1 (B), R9.2, U5.6
unnamed: Q9.3 (C), R11.2, U7.2 (IN)
unnamed: Q10.1 (B), R10.2, U6.6
unnamed: Q10.3 (C), R12.2, U7.3 (~SD)
unnamed: Q11.1 (B), R15.2, U8.6
unnamed: Q11.3 (C), R17.2, U10.2 (IN)
unnamed: Q12.1 (B), R16.2, U9.6
unnamed: Q12.3 (C), R18.2, U10.3 (~SD)
unnamed: R13.1, U7.7 (HO)
unnamed: R14.1, U7.5 (LO)
unnamed: R19.1, U10.7 (HO)
unnamed: R20.1, U10.5 (LO)
Signal_V_In: U5.2; also elsewhere on the board
Signal_V_Sd: U6.2; also elsewhere on the board
Signal_W_In: U8.2; also elsewhere on the board
Signal_W_Sd: U9.2; also elsewhere on the board



Board: 2 copper layers, 100.0 x 76.2 mm, 58 parts (6 on the bottom side), 43 nets.

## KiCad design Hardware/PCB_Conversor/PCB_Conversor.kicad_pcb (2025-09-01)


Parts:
12V_PwrCnv1: Conn_01x02; JST_XH_B2B-XH-A_1x02_P2.50mm_Vertical
C3, C4: 4700uF; CP_Radial_D16.0mm_P7.50mm
C5: 100uF; CP_Radial_D22.0mm_P10.00mm_SnapIn
D2, D4, D5: MUR860; TO-220-2_Horizontal_TabUp
D3: MUR860CT; TO-220-3_Horizontal_TabUp
D6: LED_Green; LED_0603_1608Metric_Pad1.05x0.95mm_HandSolder
F1, F2: Fuse; Fuse Holder XF-509P
HMI_Signal_B1: Conn_01x05; JST_XH_B5B-XH-A_1x05_P2.50mm_Vertical
HVDCBus_A1: Conn_01x02; PhoenixContact_MSTBVA_2,5_2-G-5,08_1x02_P5.08mm_Vertical
L1: L; L_Toroid_Vertical_L21.6mm_W8.4mm_P8.38mm_Pulse_G
Pwr+1, Pwr+2: Conn_01x01_Pin; 5mm cable solder join
Pwr-1, Pwr-2: Conn_01x01_Pin; 5mm cable solder join
R2: 1.2k; R_0603_1608Metric_Pad0.98x0.95mm_HandSolder
TP1, TP2, TP3, TP4, TP5, TP6, TP7, TP8, TP9: TestPoint; TestPoint_Loop_D2.60mm_Drill1.6mm_Beaded
TR1: Pushpull_DualPrimary; EDT36 11

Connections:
3V3_HMI: HMI_Signal_B1.5; also elsewhere on the board
5V_HMI: HMI_Signal_B1.1; also elsewhere on the board
12V_Cnv: 12V_PwrCnv1.2, D6.2 (A); also elsewhere on the board
/Conversor/Gnd_Inv: C5.2, D2.2 (A), D4.2 (A), HVDCBus_A1.2, TP5.1; also elsewhere on the board
/Conversor/Medición corriente/Current_In: D5.1 (K); also elsewhere on the board
/Conversor/Modulo conmutador pushpull1/Load: TP2.1, TR1.2; also elsewhere on the board
/Conversor/Modulo conmutador pushpull/Load: TP3.1, TR1.1; also elsewhere on the board
GND_Cnv: 12V_PwrCnv1.1, C3.2, C4.2, Pwr-1.1, Pwr-2.1, R2.2, TP1.1; also elsewhere on the board
GND_HMI: HMI_Signal_B1.2; also elsewhere on the board
Gate_Input_A: TP6.1; also elsewhere on the board
Gate_Input_B: TP7.1; also elsewhere on the board
unnamed: C3.1, F1.2, TR1.3
unnamed: C4.1, F2.2, TR1.4
unnamed: D2.1 (K), D3.1 (A1), TR1.5
unnamed: D3.3 (A2), D4.1 (K), TR1.6
unnamed: D3.2 (K), L1.1
unnamed: C5.1, D5.2 (A), L1.2, TP4.1
unnamed: D6.1 (K), R2.1
unnamed: F1.1, Pwr+1.1
unnamed: F2.1, Pwr+2.1
VSens_Corriente: HMI_Signal_B1.3, TP9.1; also elsewhere on the board
V_HVBus: HVDCBus_A1.1, TP8.1; also elsewhere on the board
Vsens_HV_HMI: HMI_Signal_B1.4; also elsewhere on the board

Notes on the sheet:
Comprar terminales (Ojal para los cables)


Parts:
C17: 10nF; C_0603_1608Metric_Pad1.08x0.95mm_HandSolder
R1, R4, R34: 150k; R_0603_1608Metric_Pad0.98x0.95mm_HandSolder
R35, R40: 10k; R_0603_1608Metric_Pad0.98x0.95mm_HandSolder
R36, R37, R38: 220k; R_0603_1608Metric_Pad0.98x0.95mm_HandSolder
R39: 4.7k; R_0603_1608Metric_Pad0.98x0.95mm_HandSolder
U13: TL431PK; SOT-89-3_Handsoldering
U14: PC817; DIP-4_W7.62mm_SMDSocket_SmallPads

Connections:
/Conversor/Gnd_Inv: R35.2, U13.2 (A); also elsewhere on the board
GND_Cnv: R39.2; also elsewhere on the board
unnamed: C17.2, R38.1, U14.1
unnamed: R1.1, R34.2
unnamed: R4.2, R34.1
unnamed: R36.1, R37.2
unnamed: R37.1, R38.2
unnamed: R39.1, R40.1, U14.3
unnamed: U13.3 (K), U14.2
unnamed: C17.1, R1.2, R35.1, U13.1 (REF)
V_HVBus: R4.1, R36.2; also elsewhere on the board
Vref_5V: U14.4; also elsewhere on the board
Vsens_HVDCBus: R40.2; also elsewhere on the board

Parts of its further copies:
C18: 10nF; C_0603_1608Metric_Pad1.08x0.95mm_HandSolder
R3, R5, R41: 150k; R_0603_1608Metric_Pad0.98x0.95mm_HandSolder
R42, R47: 10k; R_0603_1608Metric_Pad0.98x0.95mm_HandSolder
R43, R44, R45: 220k; R_0603_1608Metric_Pad0.98x0.95mm_HandSolder
R46: 4.7k; R_0603_1608Metric_Pad0.98x0.95mm_HandSolder
U15: TL431PK; SOT-89-3_Handsoldering
U16: PC817; DIP-4_W7.62mm_SMDSocket_SmallPads

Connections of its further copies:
3V3_HMI: U16.4; also elsewhere on the board
/Conversor/Gnd_Inv: R42.2, U15.2 (A); also elsewhere on the board
GND_Cnv: R46.2; also elsewhere on the board
unnamed: C18.2, R45.1, U16.1
unnamed: R3.1, R41.2
unnamed: R5.2, R41.1
unnamed: R43.1, R44.2
unnamed: R44.1, R45.2
unnamed: R46.1, R47.1, U16.3
unnamed: U15.3 (K), U16.2
unnamed: C18.1, R3.2, R42.1, U15.1 (REF)
V_HVBus: R5.1, R43.2; also elsewhere on the board
Vsens_HV_HMI: R47.2; also elsewhere on the board


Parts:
R22: 1k; R_0603_1608Metric_Pad0.98x0.95mm_HandSolder

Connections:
/Conversor/Modulo conmutador pushpull/Conmutador de potencia/GateInput: R22.2; also elsewhere on the board
Gate_Input_B: R22.1; also elsewhere on the board

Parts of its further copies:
R24: 1k; R_0603_1608Metric_Pad0.98x0.95mm_HandSolder

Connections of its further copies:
/Conversor/Modulo conmutador pushpull1/Conmutador de potencia/GateInput: R24.2; also elsewhere on the board
Gate_Input_A: R24.1; also elsewhere on the board


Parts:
C12: 1nF; C_0603_1608Metric_Pad1.08x0.95mm_HandSolder
C13: 100nF; C_0603_1608Metric_Pad1.08x0.95mm_HandSolder
D10: BZV55C3V3; D_MiniMELF_Handsoldering
R27: 221; R_0603_1608Metric_Pad0.98x0.95mm_HandSolder
U11: ACS712xLCTR-05B; SOIC-8_3.9x4.9mm_P1.27mm

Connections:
5V_HMI: C13.1, U11.8 (VCC); also elsewhere on the board
/Conversor/Medición corriente/Current_In: U11.3 (IP-), U11.4 (IP-); also elsewhere on the board
GND_HMI: C12.2, C13.2, D10.2 (A), U11.5 (GND); also elsewhere on the board
unnamed: C12.1, U11.6 (FILTER)
unnamed: R27.1, U11.7 (VIOUT)
VSens_Corriente: D10.1 (K), R27.2; also elsewhere on the board
V_HVBus: U11.1 (IP+), U11.2 (IP+); also elsewhere on the board


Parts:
C14: 100nF; C_0603_1608Metric_Pad1.08x0.95mm_HandSolder
C15: 2.2nF; C_0603_1608Metric_Pad1.08x0.95mm_HandSolder
C16: 10uF; CP_Elec_4x5.4
R28: 1.2k; R_0603_1608Metric_Pad0.98x0.95mm_HandSolder
R29: 3.9k; R_0603_1608Metric_Pad0.98x0.95mm_HandSolder
R30, R31: 10k; R_0603_1608Metric_Pad0.98x0.95mm_HandSolder
R32, R33: 1k; R_0603_1608Metric_Pad0.98x0.95mm_HandSolder
RV1, RV2: 5K; Potentiometer_Bourns_3314S_Horizontal
U12: TL494; SOIC-16_3.9x9.9mm_P1.27mm

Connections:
12V_Cnv: C16.1, U12.8 (C1), U12.11 (C2), U12.12 (VCC); also elsewhere on the board
DeadTimeControl: C14.1, R30.1, U12.4 (DTC)
GND_Cnv: C15.1, C16.2, R29.2, R30.2, R31.2, R32.1, R33.1, RV2.3, U12.7 (GND); also elsewhere on the board
Gate_Input_A: R32.2, U12.9 (E1); also elsewhere on the board
Gate_Input_B: R33.2, U12.10 (E2); also elsewhere on the board
unnamed: R28.2, RV1.1
unnamed: R29.1, RV1.3
unnamed: U12.3 (FB), U12.15 (2IN-)
unnamed: C15.2, U12.5 (CT)
unnamed: R31.1, U12.6 (RT)
Vref_5V: C14.2, R28.1, RV2.1, U12.13 (OUTCTRL), U12.14 (REF); also elsewhere on the board
Vref_In1: RV1.2, U12.2 (1IN-)
Vref_In2: RV2.2, U12.16 (2IN+)
Vsens_HVDCBus: U12.1 (1IN+); also elsewhere on the board


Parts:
Q13: SS8050; SOT-23
Q14: SS8550; SOT-23
Q15: IRFB4110PBF; TO-220-3_Horizontal_TabUp
R21: 10; R_0603_1608Metric_Pad0.98x0.95mm_HandSolder

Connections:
12V_Cnv: Q13.3 (C); also elsewhere on the board
/Conversor/Modulo conmutador pushpull/Conmutador de potencia/GateInput: Q13.1 (B), Q14.1 (B); also elsewhere on the board
/Conversor/Modulo conmutador pushpull/Load: Q15.2 (D); also elsewhere on the board
GND_Cnv: Q14.3 (C), Q15.3 (S); also elsewhere on the board
unnamed: Q13.2 (E), Q14.2 (E), R21.1
unnamed: Q15.1 (G), R21.2

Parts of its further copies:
Q16, Q19, Q22: SS8050; SOT-23
Q17, Q20, Q23: SS8550; SOT-23
Q18, Q21, Q24: IRFB4110PBF; TO-220-3_Horizontal_TabUp
R23, R25, R26: 10; R_0603_1608Metric_Pad0.98x0.95mm_HandSolder

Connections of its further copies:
12V_Cnv: Q16.3 (C), Q19.3 (C), Q22.3 (C); also elsewhere on the board
/Conversor/Modulo conmutador pushpull1/Conmutador de potencia/GateInput: Q19.1 (B), Q20.1 (B), Q22.1 (B), Q23.1 (B); also elsewhere on the board
/Conversor/Modulo conmutador pushpull1/Load: Q21.2 (D), Q24.2 (D); also elsewhere on the board
/Conversor/Modulo conmutador pushpull/Conmutador de potencia/GateInput: Q16.1 (B), Q17.1 (B); also elsewhere on the board
/Conversor/Modulo conmutador pushpull/Load: Q18.2 (D); also elsewhere on the board
GND_Cnv: Q17.3 (C), Q18.3 (S), Q20.3 (C), Q21.3 (S), Q23.3 (C), Q24.3 (S); also elsewhere on the board
unnamed: Q16.2 (E), Q17.2 (E), R23.1
unnamed: Q18.1 (G), R23.2
unnamed: Q19.2 (E), Q20.2 (E), R25.1
unnamed: Q21.1 (G), R25.2
unnamed: Q22.2 (E), Q23.2 (E), R26.1
unnamed: Q24.1 (G), R26.2

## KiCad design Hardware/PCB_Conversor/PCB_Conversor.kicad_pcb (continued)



Board: 2 copper layers, 100.0 x 100.0 mm, 88 parts (36 on the bottom side), 61 nets.

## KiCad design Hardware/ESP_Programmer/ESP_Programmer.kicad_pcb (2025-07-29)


Board: 2 copper layers, 33.8 x 24.1 mm, 16 parts (0 on the bottom side), 14 nets.

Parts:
C1, C2: 1nF; C_0603_1608Metric
C13, C14: 1uF; C_0603_1608Metric
D1, D2: LED; LED_0603_1608Metric_Pad1.05x0.95mm_HandSolder
J1: Conn_01x05_Pin; PinHeader_1x05_P2.00mm_Vertical_SMD_Pin1Right
J2: USB_OTG; USB_Mini-B_Tensility_54-00023_Vertical
R1, R2, R8, R9: 221; R_0603_1608Metric
SW9, SW10: SW_MEC_5E; SW_MEC_5GSH9
U1: CH340C; SOIC-16_3.9x9.9mm_P1.27mm
U3: AMS1117-3.3; SOT-223-3_TabPin2

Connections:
+3.3V: C2.1, C14.1, R1.1, R2.1, U1.16 (VCC), U3.2 (VO)
+5V: C13.1, J2.1 (VBUS), U3.3 (VI)
/BOOT_prog: J1.2, R9.1
/ENABLE: J1.3, R8.1
/Rx: D2.1 (K), J1.4, U1.3 (RXD)
/Tx: D1.1 (K), J1.5, U1.2 (TXD)
GND: C1.1, C2.2, C13.2, C14.2, J1.1, J2.5 (GND), J2.6 (Shield), SW9.1, SW9.2, SW10.1, SW10.2, U1.1 (GND), U3.1 (GND)
unnamed: D1.2 (A), R1.2
unnamed: D2.2 (A), R2.2
unnamed: J2.3 (D+), U1.5 (UD+)
unnamed: J2.2 (D-), U1.6 (UD-)
unnamed: R8.2, SW9.3 (K), SW9.4 (A)
unnamed: R9.2, SW10.3 (K), SW10.4 (A)
unnamed: C1.2, U1.4 (V3)

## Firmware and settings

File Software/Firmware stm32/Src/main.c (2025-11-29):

/**
 * @file main.c
 * @brief Punto de entrada del firmware y configuración de periféricos.
 * @details Inicializa reloj de sistema, GPIO, DMA, SPI2 (esclavo), USART1 (debug),
 *          y TIM2/TIM3 (cálculo y switching). Integra módulos GestorSVM, GestorTimers,
 *          GestorEstados y SPI module.
 *   Disposicion de transistores, los transistores
 *   son los Q1, Q2, Q3, Q4, Q5 y Q6 
 *   |    |    |
 *   Q1   Q2   Q3
 *   |    |    |
 *   |    |    |
 *   Q4   Q5   Q6
 *   |    |    | 
 *   Como esto esta controlado por drivers de mosfets, entonces vamos a poner un 1 para activar el transistor superior y un cero para el transistor inferior.
 *   Vamos a tener ocho vectores en que vamos a trabajar: v0, v1, v2, v3, v4, v5, v6 y v7. Siendo el v0 y v7 dos vectores nulos. Cada uno de estos cuadrantes tiene un valor que indica el valor de los transistores:
 * - v0 = 000,
 * - v1 = 001,
 * - v2 = 010,
 * - v3 = 011,
 * - v4 = 100,
 * - v5 = 101, 
 * - v6 = 110,
 * - v7 = 111.
 *  Ahora vamos a detallar por cuadrante como nos va a quedar y que cambia en cada cuadrante  
 * - Quad 1: v0, v1, v3, v7  => P3: High, P2: High, P1: High, P1: Low, P2: Low, P3: Low
 * - Quad 2: v0, v2, v3, v7  => P2: High, P3: High, P1: High, P1: Low, P3: Low, P2: Low
 * - Quad 3: v0, v2, v6, v7  => P2: High, P1: High, P3: High, P3: Low, P1: Low, P2: Low
 * - Quad 4: v0, v4, v6, v7  => P1: High, P2: High, P3: High, P3: Low, P2: Low, P1: Low
 * - Quad 5: v0, v4, v5, v7  => P1: High, P3: High, P2: High, P2: Low, P3: Low, P1: Low
 * - Quad 6: v0, v1, v5, v7  => P3: High, P1: High, P2: High, P2: Low, P1: Low, P3: Low
 */

#include "main.h"
#include <stdio.h>

#include "../Modules/Gestor_SVM/GestorSVM.h"
#include "../Modules/Gestor_Timers/GestorTimers.h"
#include "../Modules/Gestor_Estados/GestorEstados.h"
#include "../Modules/SPI_Interfase/SPIModule.h"

SPI_HandleTypeDef hspi2;
DMA_HandleTypeDef hdma_spi2_tx;
DMA_HandleTypeDef hdma_spi2_rx;
TIM_HandleTypeDef htim2;
TIM_HandleTypeDef htim3;
UART_HandleTypeDef huart1;

/**
 * @fn static void SystemClock_Config(void)
 * @brief Configura el clock del sistema a 72 MHz desde HSE=8 MHz con PLL×9.
 * @details Activa HSE, configura PLL (source=HSE, mul=×9) y selecciona SYSCLK=PLL.
 *          AHB=72 MHz, APB2=72 MHz (div1), APB1=36 MHz (div2), FLASH_LATENCY=2.
 */
 static void SystemClock_Config(void);

/**
 * @fn static void MX_GPIO_Init(void);
 * 
 * @brief Inicializa GPIOA y GPIOB.
 *
 * @details Configura los pines de los puertos A y B como salidas push pull, sin pull up y como pines de baja frecuencia. Los pines configurados son los que controlan el modulador y salidas (leds de estado). Las entradas digitales (termoswitch y boton de stop) no son configuradas ya que serán señales controladas por el HMI.
 */
static void MX_GPIO_Init(void);

/**
 * @fn static void MX_DMA_Init(void)
 *
 * @brief Habilita el clock del DMA1 y sus interrupciones de canal 4 y 5.
 *
 * @details Habilita el reloj del **DMA1** y registra en el NVIC las IRQ de **DMA1_Channel4** y **DMA1_Channel5** con prioridad 2.
 * En F1, estos canales suelen mapearse a **SPI2_RX (Ch4)** y **SPI2_TX (Ch5)**, por lo que esta rutina deja listo el DMA para que llamadas como `HAL_SPI_TransmitReceive_DMA()` configuren y lancen las transferencias.  
 * No configura direcciones, tamaños ni modos del DMA; solo habilita el clock y las IRQ.
 * @note Anteriormente la prioridad era 0. Luego pasó a 2 ya que en el SPI se configura en 2.
 */
static void MX_DMA_Init(void);

/**
 * @fn  static void MX_TIM3_Init(void);
 * 
 * @brief Función inicialización del timer 3 (SVM)
 *
 * @details El timer 3 es utilizado para ejecutar el swtching de los pines del variador de frecuencia. Trabaja con un timer de 0 a 256 utilizando el clock interno como fuente de conteo dando un período de 398.22us (f = 2511Hz) y 4 canales de interrupción CCR1-4 que se irán corriendo conforme vaya avanzando la señal y cambiando la tensión de salida buscada de acuerdo a lo que dicte el estado del módulo SVM.
 */
static void MX_TIM3_Init(void);

/**
  * @fn static void MX_TIM2_Init(void);
  * 
  * @brief Función de inicialización del timer 2 (Pre cálculo)
  *
  * @details El timer funcionará a 10KHz tratando de adelantar los cálculos del timer 3, permitiendo agilizar la carga de sus contadores y evitando que haya problemas en la señal de salida.
  */
static void MX_TIM2_Init(void);

/**
  * @fn static void MX_USART1_UART_Init(void);
  *
  * @brief Inicialización de la UART 1 (DEBUG)
  *
  * @details El periférico se utilizará como puerto de debug. Solo tendrá pines de transmisión y recepción sin control de flujo; con configuración 115200,8,N,1
  */
static void MX_USART1_UART_Init(void);

/**
  * @fn static void MX_SPI2_Init(void);
  * 
  * @brief SPI2 Initialization Function (HMI)
  *
  * @details Configura al SPI2 como esclavo, dependiendo de la comuincación con el maestro, el ESP32 para poder transaccionar información. Inicializa un tamaño de 8 bits de datos, con dos líneas de comunicación (MISO y MOSI) comenzando el byte por bit más gignificativo. No utiliza el módulo CRC, el latch del dato se toma en el flanco decreciente del clock y la línea en reposo queda en estado alto. El pin de selección de esclavo es utilizado por el maestro para iniciar la comunicación.
  */
static void MX_SPI2_Init(void);

/**
 * @brief 
 * 
 * @brief  Función de entrada del sistema
 *
 * @details
 * La función main inicializa la estructura de configuración, inicializa los periféricos y el gestor de estados. Al terminar su trabajo queda en un while(1) con la sentencia WFI para reducir el consumo de CPU.
 *   1) HAL_Init()
 *   2) SystemClock_Config()
 *   3) Carga configuración SVM (frecuencia de switching, ref, etc.).
 *   4) Inicializa manejador de timers (GestorTimers_Init).
 *   5) Inicializa periféricos (GPIO, DMA, TIM3, USART1, TIM2, SPI2) y driver SPI.
 *   6) Notifica fin de init al Gestor de Estados (ACTION_INIT_DONE).
 *   7) Entra en lazo con WFI para ahorrar CPU, atendiendo a interrupciones.
 *
  * @retval int
 *     Sin uso
  */
int main(void) {

  HAL_Init();                                   /// Configuración del MCU. Reset of all peripherals, Initializes the Flash interface and the Systick.
  SystemClock_Config();
 
  
  ConfiguracionSVM config = {                   /// Cofiguración del módulo SVM
    .frec_switch = 2511,                        /// Frecuencia de 2.511kHz para el switch del timer 3 entre subida y bajada del timer 3
    .frecReferencia = 50,                       /// Frecuencia de salida
    .direccionRotacion = 1,                     /// Sentido horario
    .acel = 5,                                  /// Aceleracón del sistema por default [Hz/seg]
    .desacel = 3,                               /// Desaceleracón del sistema por default [Hz/seg]
  };
  
  // Cargamos los numeros de los pines
  config.puerto_senal_pierna[0] = GPIO_PIN_1;
  config.puerto_senal_pierna[1] = GPIO_PIN_3;
  config.puerto_senal_pierna[2] = GPIO_PIN_5;
  config.puerto_encen_pierna[0] = GPIO_PIN_2;
  config.puerto_encen_pierna[1] = GPIO_PIN_4;
  config.puerto_encen_pierna[2] = GPIO_PIN_6;
  GestorSVM_SetConfiguration(&config);

  // Initialize all configured peripherals
  MX_GPIO_Init();
  MX_DMA_Init();
  MX_TIM3_Init();
  MX_TIM2_Init();
  MX_USART1_UART_Init();
  MX_SPI2_Init();
  SPI_Init(&hspi2);

  // Inicio del gestor de timers
  GestorTimers_Init(&htim3, &htim2);

  // Informamos al gestor de estados que finalizo la inicializacion
  // Esta debe ser la ultima llama de funcion del init
  GestorEstados_Action(ACTION_INIT_DONE, 0);
  printf("Config done\n");

  __HAL_DBGMCU_FREEZE_TIM3();
  __HAL_DBGMCU_FREEZE_TIM2();

  while (1) {
    __WFI();
  }
}

static void SystemClock_Config(void) {
  RCC_OscInitTypeDef RCC_OscInitStruct = {0};
  RCC_ClkInitTypeDef RCC_ClkInitStruct = {0};

  // Initializes the RCC Oscillators according to the specified parameters in the RCC_OscInitTypeDef structure.
  RCC_OscInitStruct.OscillatorType = RCC_OSCILLATORTYPE_HSE;
  RCC_OscInitStruct.HSEState = RCC_HSE_ON;
  RCC_OscInitStruct.HSEPredivValue = RCC_HSE_PREDIV_DIV1;
  RCC_OscInitStruct.HSIState = RCC_HSI_ON;
  RCC_OscInitStruct.PLL.PLLState = RCC_PLL_ON;
  RCC_OscInitStruct.PLL.PLLSource = RCC_PLLSOURCE_HSE;
  RCC_OscInitStruct.PLL.PLLMUL = RCC_PLL_MUL9;
  if (HAL_RCC_OscConfig(&RCC_OscInitStruct) != HAL_OK) {
    Error_Handler();
  }

  // Initializes the CPU, AHB and APB buses clocks
  RCC_ClkInitStruct.ClockType = RCC_CLOCKTYPE_HCLK|RCC_CLOCKTYPE_SYSCLK|RCC_CLOCKTYPE_PCLK1|RCC_CLOCKTYPE_PCLK2;
  RCC_ClkInitStruct.SYSCLKSource = RCC_SYSCLKSOURCE_PLLCLK;
  RCC_ClkInitStruct.AHBCLKDivider = RCC_SYSCLK_DIV1;
  RCC_ClkInitStruct.APB1CLKDivider = RCC_HCLK_DIV2;
  RCC_ClkInitStruct.APB2CLKDivider = RCC_HCLK_DIV1;

  if (HAL_RCC_ClockConfig(&RCC_ClkInitStruct, FLASH_LATENCY_2) != HAL_OK) {
    Error_Handler();
  }
}

static void MX_SPI2_Init(void) {
  hspi2.Instance = SPI2;
  hspi2.Init.Mode = SPI_MODE_SLAVE;
  hspi2.Init.Direction = SPI_DIRECTION_2LINES;
  hspi2.Init.DataSize = SPI_DATASIZE_8BIT;
  hspi2.Init.CLKPolarity = SPI_POLARITY_LOW;
  hspi2.Init.CLKPhase = SPI_PHASE_1EDGE;
  hspi2.Init.NSS = SPI_NSS_HARD_INPUT;
  hspi2.Init.FirstBit = SPI_FIRSTBIT_MSB;
  hspi2.Init.TIMode = SPI_TIMODE_DISABLE;
  hspi2.Init.CRCCalculation = SPI_CRCCALCULATION_DISABLE;
  hspi2.Init.CRCPolynomial = 10;
  if (HAL_SPI_Init(&hspi2) != HAL_OK) {
    Error_Handler();
  }
}

static void MX_TIM2_Init(void) {

  TIM_ClockConfigTypeDef sClockSourceConfig = {0};
  TIM_MasterConfigTypeDef sMasterConfig = {0};
  TIM_OC_InitTypeDef sConfigOC = {0};

  htim2.Instance = TIM2;
  htim2.Init.Prescaler = 0;
  htim2.Init.CounterMode = TIM_COUNTERMODE_UP;
  htim2.Init.Period = 7199;
  htim2.Init.ClockDivision = TIM_CLOCKDIVISION_DIV1;
  htim2.Init.AutoReloadPreload = TIM_AUTORELOAD_PRELOAD_DISABLE;
  if (HAL_TIM_Base_Init(&htim2) != HAL_OK) {
    Error_Handler();
  }

  sClockSourceConfig.ClockSource = TIM_CLOCKSOURCE_INTERNAL;
  if (HAL_TIM_ConfigClockSource(&htim2, &sClockSourceConfig) != HAL_OK) {
    Error_Handler();
  }
  if (HAL_TIM_OC_Init(&htim2) != HAL_OK) {
    Error_Handler();
  }

  sMasterConfig.MasterOutputTrigger = TIM_TRGO_RESET;
  sMasterConfig.MasterSlaveMode = TIM_MASTERSLAVEMODE_DISABLE;
  if (HAL_TIMEx_MasterConfigSynchronization(&htim2, &sMasterConfig) != HAL_OK) {
    Error_Handler();
  }

  sConfigOC.OCMode = TIM_OCMODE_TIMING;
  sConfigOC.Pulse = 5;
  sConfigOC.OCPolarity = TIM_OCPOLARITY_HIGH;
  sConfigOC.OCFastMode = TIM_OCFAST_DISABLE;
  if (HAL_TIM_OC_ConfigChannel(&htim2, &sConfigOC, TIM_CHANNEL_1) != HAL_OK) {
    Error_Handler();
  }
}

static void MX_TIM3_Init(void) {
  TIM_ClockConfigTypeDef sClockSourceConfig = {0};
  TIM_MasterConfigTypeDef sMasterConfig = {0};
  TIM_OC_InitTypeDef sConfigOC = {0};

  htim3.Instance = TIM3;
  htim3.Init.Prescaler = 55;
  htim3.Init.CounterMode = TIM_COUNTERMODE_CENTERALIGNED3;
  htim3.Init.Period = 256;
  htim3.Init.ClockDivision = TIM_CLOCKDIVISION_DIV1;
  htim3.Init.AutoReloadPreload = TIM_AUTORELOAD_PRELOAD_ENABLE;
  if (HAL_TIM_Base_Init(&htim3) != HAL_OK) {
    Error_Handler();
  }

  sClockSourceConfig.ClockSource = TIM_CLOCKSOURCE_INTERNAL;
  if (HAL_TIM_ConfigClockSource(&htim3, &sClockSourceConfig) != HAL_OK) {
    Error_Handler();
  }
  if (HAL_TIM_OC_Init(&htim3) != HAL_OK) {
    Error_Handler();
  }

  sMasterConfig.MasterOutputTrigger = TIM_TRGO_RESET;
  sMasterConfig.MasterSlaveMode = TIM_MASTERSLAVEMODE_DISABLE;
  if (HAL_TIMEx_MasterConfigSynchronization(&htim3, &sMasterConfig) != HAL_OK) {
    Error_Handler();
  }

  sConfigOC.OCMode = TIM_OCMODE_TIMING;
  sConfigOC.Pulse = 0;
  sConfigOC.OCPolarity = TIM_OCPOLARITY_HIGH;
  sConfigOC.OCFastMode = TIM_OCFAST_DISABLE;
  if (HAL_TIM_OC_ConfigChannel(&htim3, &sConfigOC, TIM_CHANNEL_1) != HAL_OK)
  {
    Error_Handler();
  }
  __HAL_TIM_ENABLE_OCxPRELOAD(&htim3, TIM_CHANNEL_1);
  sConfigOC.Pulse = 20;
  if (HAL_TIM_OC_ConfigChannel(&htim3, &sConfigOC, TIM_CHANNEL_2) != HAL_OK)
  {
    Error_Handler();
  }
  __HAL_TIM_ENABLE_OCxPRELOAD(&htim3, TIM_CHANNEL_2);
  sConfigOC.Pulse = 80;
  if (HAL_TIM_OC_ConfigChannel(&htim3, &sConfigOC, TIM_CHANNEL_3) != HAL_OK)
  {
    Error_Handler();
  }
  __HAL_TIM_ENABLE_OCxPRELOAD(&htim3, TIM_CHANNEL_3);
  sConfigOC.Pulse = 240;
  if (HAL_TIM_OC_ConfigChannel(&htim3, &sConfigOC, TIM_CHANNEL_4) != HAL_OK)
  {
    Error_Handler();
  }
  __HAL_TIM_ENABLE_OCxPRELOAD(&htim3, TIM_CHANNEL_4);

}

static void MX_USART1_UART_Init(void) {
  huart1.Instance = USART1;
  huart1.Init.BaudRate = 115200;
  huart1.Init.WordLength = UART_WORDLENGTH_8B;
  huart1.Init.StopBits = UART_STOPBITS_1;
  huart1.Init.Parity = UART_PARITY_NONE;
  huart1.Init.Mode = UART_MODE_TX_RX;
  huart1.Init.HwFlowCtl = UART_HWCONTROL_NONE;
  huart1.Init.OverSampling = UART_OVERSAMPLING_16;
  if (HAL_UART_Init(&huart1) != HAL_OK) {
    Error_Handler();
  }
}

static void MX_DMA_Init(void) {
  __HAL_RCC_DMA1_CLK_ENABLE();
  HAL_NVIC_SetPriority(DMA1_Channel4_IRQn, 2, 0);
  HAL_NVIC_EnableIRQ(DMA1_Channel4_IRQn);
  HAL_NVIC_SetPriority(DMA1_Channel5_IRQn, 2, 0);
  HAL_NVIC_EnableIRQ(DMA1_Channel5_IRQn);
}

static void MX_GPIO_Init(void) {
  GPIO_InitTypeDef GPIO_InitStruct = {0};

  /* GPIO Ports Clock Enable */
  __HAL_RCC_GPIOD_CLK_ENABLE();
  __HAL_RCC_GPIOA_CLK_ENABLE();
  __HAL_RCC_GPIOB_CLK_ENABLE();

  HAL_GPIO_WritePin(GPIOA, GPIO_U_IN|GPIO_U_SD|GPIO_V_IN|GPIO_V_SD|GPIO_W_IN|GPIO_W_SD, GPIO_PIN_RESET);//|GPIO_TERMO_SWITCH|GPIO_STOP_BUTTON, GPIO_PIN_RESET);
  HAL_GPIO_WritePin(GPIOB, GPIO_LED_STATE|GPIO_LED_ERROR, GPIO_PIN_RESET);

  GPIO_InitStruct.Pin = GPIO_U_IN|GPIO_U_SD|GPIO_V_IN|GPIO_V_SD|GPIO_W_IN|GPIO_W_SD|GPIO_TERMO_SWITCH|GPIO_STOP_BUTTON;
  GPIO_InitStruct.Mode = GPIO_MODE_OUTPUT_PP;
  GPIO_InitStruct.Pull = GPIO_NOPULL;
  GPIO_InitStruct.Speed = GPIO_SPEED_FREQ_LOW;
  HAL_GPIO_Init(GPIOA, &GPIO_InitStruct);

  GPIO_InitStruct.Pin = GPIO_LED_STATE|GPIO_LED_ERROR;
  GPIO_InitStruct.Mode = GPIO_MODE_OUTPUT_PP;
  GPIO_InitStruct.Pull = GPIO_NOPULL;
  GPIO_InitStruct.Speed = GPIO_SPEED_FREQ_LOW;
  HAL_GPIO_Init(GPIOB, &GPIO_InitStruct);
}

/**
 * @fn void Error_Handler(void);
 * @fn void Error_Handler(void)
 * @brief Manejador genérico de errores.
 * @details Deshabilita IRQs y entra en bucle infinito para provocar reset por IWDG si está activo.
 */
void Error_Handler(void) {
  __disable_irq();
  while (1) {
  }
}

#ifdef  USE_FULL_ASSERT
/**
  * @fn  void assert_failed(uint8_t *file, uint32_t line);
  * @brief  Reporta el nombre del archivo fuente y su línea donde un assert_param falla.
  * @param  file: Puntero al nombre del archivo fuente.
  * @param  line: Número de línea del assert_param que falló
  */
void assert_failed(uint8_t *file, uint32_t line);
void assert_failed(uint8_t *file, uint32_t line) {
  printf("Wrong parameters value: file %s on line %d\r\n", file, line)
}
#endif /* USE_FULL_ASSERT */

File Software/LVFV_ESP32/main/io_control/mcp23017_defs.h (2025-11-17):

#ifndef __MCP23017_DEFS_H__

#define __MCP23017_DEFS_H__

#include <inttypes.h>
#include <stdio.h>
#include <stdlib.h>
#include <stdbool.h>
#include <stdbool.h>

#define __MCP23017_BANK_SEQUENTIAL__            0                           /*!< Modo de banqueo de moemora separado por puertos */
#define __MCP23017_BANK_SPLIT__                 1                           /*!< Modo de banqueo de moemora entrelazando puertos para manejo con entreos de 16 bits */

#define __MCP23017_MIRROR_UNCONNECTED__         0                           /*!< Los pines de interrupción no están internamente conectados */
#define __MCP23017_MIRROR_CONNECTED__           1                           /*!< Los pines de interrupción están internamente conectados */

#define __MCP23017_SEQOP_ENABLED__              0                           /*!< El puntero de direccionamiento de memoria incrementa en cada acceso */
#define __MCP23017_SEQOP_DISABLED__             1                           /*!< El puntero de direccionamiento de memoria no incrementa en cada acceso */

#define __MCP23017_DISSLW_DISABLED__            0                           /*!< Slew rate deshabilitado */
#define __MCP23017_DISSLW_ENABLED__             1                           /*!< Slew rate habilitado */

#define __MCP23017_ODR_OPEN_DRAIN_OUTPUT__      1                           /*!< Flags de interrupción de los puerto A y B configuradas open drain */
#define __MCP23017_ODR_ACTIVE_DRIVER_OUTPUT__   0                           /*!< Flags de interrupción de los puerto A y B configuradas como salidas activas */

#define __MCP23017_INTPOL_POLARITY_LOW__        1                           /*!< Flags de interrupción de los puerto A y B en 0 significa una nueva interrupción*/
#define __MCP23017_INTPOL_POLARITY_HIGH__       0                           /*!< Flags de interrupción de los puerto A y B en 1 significa una nueva interrupción*/

#define __MCP23017_GPPU_PULL_UP_ENABLE__        1                           /*!< Activación de pull up de GPIO */
#define __MCP23017_GPPU_PULL_UP_DISABLE__       0                           /*!< DESctivación de pull up de GPIO */

#define __MCP23017_IODIR_INPUT__                1                           /*!< GPIO configurada como entrada */
#define __MCP23017_IODIR_OUTPUT__               0                           /*!< GPIO configurada como salida */

#define __MCP23017_GPINTEN_ENABLE__             1                           /*!< Interrupción de GPIO habilitada */
#define __MCP23017_GPINTEN_DISABLE__            0                           /*!< Interrupción de GPIO deshabilitada */

#define __MCP23017_INTCON_DEFVAL__              1                           /*!< Interrupción dispara por diferencia con valor default */
#define __MCP23017_INTCON_CHANGE__              0                           /*!< Interrupción dispara por diferencia con útlimo valor */

#define __MCP23017_WRITE__                      0                           /*!< Función de escritura del MCP23017 - Se inserta en el opcode */
#define __MCP23017_READ__                       1                           /*!< Función de lectura del MCP23017 - Se inserta en el opcode */

#define __MCP23017_POSITIVE_LOGIC__             0                           /*!< Configuración de la lógica de los GPIO como positiva */
#define __MCP23017_OPPOSITE_LOGIC__             1                           /*!< Configuración de la lógica de los GPIO como negativa */

#define __MCP23017_INTERRUPT_ENABLE__           0                           /*!< Deshabilitación de la interrupción del GPIO */
#define __MCP23017_INTERRUPT_DISABLE__          1                           /*!< Habilitación de la interrupción del GPIO */

#define __MCP23017_ADDRESS__                    0b010                       /*!< CONFIGURADO POR HARDWARE: Address del MCP23017 =  0b010 ----> OPCODE: 0100AAA0 -> 01000000 | __MCP23017_ADDRESS__ << 1 | R/W */ 

#define __MCP23017_READ_OPPCODE__           0b0100 << 4 | __MCP23017_ADDRESS__ << 1 | __MCP23017_READ__     /*!< Código de operación para lectura en el MCP23017 */
#define __MCP23017_WRITE_OPPCODE__          0b0100 << 4 | __MCP23017_ADDRESS__ << 1 | __MCP23017_WRITE__    /*!< Código de operación para escritura en el MCP23017 */
#define __MCP23017_FUNC_MODE__              __MCP23017_BANK_SEQUENTIAL__                                    /*!< Modo de funcionamieto del MCP23017 que funcionará en el sistema */
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

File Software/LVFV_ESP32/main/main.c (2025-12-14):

/**
 * @file main.c
 * @author Andrenacci - Carra
 * @brief Inicialización de tareas y periféricos que no tienen una tarea específica. El resto de los periféricos se inicializan en las tareas que son utilizados.
 * @version 2.0
 * @date 2025-11-06
 * 
 */
#include <inttypes.h>
#include <time.h>
#include <sys/time.h>

#include "sdkconfig.h"
#include "freertos/FreeRTOS.h"
#include "freertos/task.h"

#include "esp_chip_info.h"
#include "esp_flash.h"
#include "esp_system.h"
#include "esp_log.h"
#include "esp_err.h"
#include "esp_sleep.h"
#include "esp_clk_tree.h"

#include "driver/gpio.h"

#include "./display/display.h"
#include "./io_control/io_control.h"
#include "./System/SysControl.h"
#include "./adc/adc.h"
#include "./nvs/nvs.h"
#include "./rtc/rtc.h"
#include "./wifi/wifi.h"

#include "LVFV_system.h"

static const char *TAG = "UTN-CA-PF2025";                       /// Tag de logs del sistema

/**
 * @brief Función principal de la aplicación
 * 
 */
void app_main(void) {

    nvs_init_once();
    if ( initRTC() == ESP_OK ) {
        ESP_LOGI(TAG, "RTC inicializado correctamente");
    } else {
        ESP_LOGE(TAG, "Error al inicializar el RTC");
        ESP_ERROR_CHECK(ESP_FAIL);
    }
    xTaskCreatePinnedToCore( task_display,                  "Tarea Display",                    4096, NULL, 10, NULL, 1);

    xTaskCreatePinnedToCore(adc_task,                       "adc_task",                         4096, NULL, 9,  NULL, 0);
    xTaskCreatePinnedToCore(SPI_communication,              "SPI_communication",                4096, NULL, 9,  NULL, 0);
    xTaskCreatePinnedToCore(GPIO_interrupt_attendance_task, "GPIO_interrupt_attendance_task",   4096, NULL, 10, NULL, 0);

    wifi_init_softap();
    // start_mdns();
    start_webserver();

    while (1) {
        vTaskDelay(pdMS_TO_TICKS(1000));
    }
}

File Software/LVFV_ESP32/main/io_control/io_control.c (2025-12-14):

/**
 * @file io_control.c
 * @author Andrenacci - Carra
 * @brief Funciones de control del relay, buzzer y tarea del uso del expansor de entradas y salidas y entradas y salidas aisladas directas al ESP32
 * @details Las tareas de relay y buzzer son tareas aisladas del resto del sistema y son accedidas a través de las funciones RelayEvantPost y BuzzerEvantPost. Esto genera que no sea necesaria que la cola de comandos deba ser utilizada en diversos archivos, pretege los valores que envía antes de generar el procesamiento del dato desde las respectivas tareas.
 Cuenta además con la selección, elección y control de entradas que le corresponde a cada tecla del teclado, cada entrada digital aislada. Trabaja con el antirrubote de las entradas, evitando que se filtren pulsos de ruido que hayan sido detectadas como cambios en las entradas o evitar que se generen más de un evento cuando en realidad era uno solo.
 También corre la tarea que controla la salida de 0 a 10 volts de contínua, la señal que representa indirectamente la frecuencia de operación del motor.
 * @version 2.0
 * @date 2025-11-06
 * 
 */
#include "sdkconfig.h"

#include "esp_err.h"
#include "esp_log.h"

#include "driver/gpio.h"
#include "driver/ledc.h"
#include "display/display.h"

#include "freertos/FreeRTOS.h"
#include "freertos/semphr.h"
#include "freertos/task.h"
#include "freertos/queue.h"

#include <inttypes.h>
#include <stdio.h>
#include <stdlib.h>

#include "mcp23017_defs.h"

#include "./MCP23017.h"
#include "./io_control.h"
#include "../system/sysAdmin.h"
#include "../system/sysControl.h"

static const char *TAG = "IO_CTRL";                                                                                     /*!< Varaible que se imprime en los ESP_LOG */

#define INT_A_PIN                   GPIO_NUM_22                                                                         /*!< Configuración de pin físico correspondiente al flag de interrupciones del puerto A del MCP23017 */

#define BUZZER_PIN                  0                                                                                   /*!< Pin del puerto A que controla el buzzer de la HMI */
#define RELAY_PIN                   1                                                                                   /*!< Pin del puerto A que controla el relé de la HMI */
#define FREQ_SEL_1_PIN              2                                                                                   /*!< Pin del puerto A que controla la selección de frecuencia 1 del variador de frecuencia */
#define FREQ_SEL_2_PIN              3                                                                                   /*!< Pin del puerto A que controla la selección de frecuencia 2 del variador de frecuencia */
#define FREQ_SEL_3_PIN              4                                                                                   /*!< Pin del puerto A que controla la selección de frecuencia 3 del variador de frecuencia */
#define STOP_PIN                    5                                                                                   /*!< Pin del puerto A que controla el botón de parada delvariador de frecuencia */
#define TERMO_SW_PIN                6                                                                                   /*!< Pin del puerto A que controla el interruptor térmico del variador de frecuencia */

#define FREQ_SEL_MASK               ( (1 << FREQ_SEL_3_PIN) | (1 << FREQ_SEL_2_PIN) | (1 << FREQ_SEL_1_PIN) )           /*!< Máscara que, comparada con el registro de flags de interrupción, permite identificar cambios en las entradas del variador de frecuencia */
#define TERMO_SW_MASK               (1 << TERMO_SW_PIN)                                                                 /*!< Máscara que, comparada con el registro de flags de interrupción, permite identificar cambios en el interruptor térmico del variador de frecuencia */
#define STOP_SW_MASK                (1 << STOP_PIN)                                                                     /*!< Máscara que, comparada con el registro de flags de interrupción, permite identificar cambios en el botón de parada del variador de frecuencia */

#define INT_B_PIN                   GPIO_NUM_23                                                                         /*!< Configuración de pin físico correspondiente al flag de interrupciones del puerto B del MCP23017 */

#define MATRIX_SW1                  0x17                                                                                /*!< Representación de switch impreso como SW1 en la serigrafía por 0x17  */
#define MATRIX_SW2                  0x27                                                                                /*!< Representación de switch impreso como SW2 en la serigrafía por 0x27  */
#define MATRIX_SW3                  0x1B                                                                                /*!< Representación de switch impreso como SW3 en la serigrafía por 0x1B  */
#define MATRIX_SW4                  0x2B                                                                                /*!< Representación de switch impreso como SW4 en la serigrafía por 0x2B  */
#define MATRIX_SW5                  0x1D                                                                                /*!< Representación de switch impreso como SW5 en la serigrafía por 0x1D  */
#define MATRIX_SW6                  0x2D                                                                                /*!< Representación de switch impreso como SW6 en la serigrafía por 0x2D  */
#define MATRIX_SW7                  0x1E                                                                                /*!< Representación de switch impreso como SW7 en la serigrafía por 0x1E  */
#define MATRIX_SW8                  0x2E                                                                                /*!< Representación de switch impreso como SW8 en la serigrafía por 0x2E  */
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

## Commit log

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2025-07-09 Subida del esquemático del HMI. Falta terminar.
    [Fuentes.kicad_sch, HMI_LVDC-Inverter.kicad_pcb, HMI_LVDC-Inverter.kicad_sch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]
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2025-07-09 Creación de carpeta de hardware
    [Fuentes.kicad_sch, HMI_LVDC-Inverter.kicad_pcb, HMI_LVDC-Inverter.kicad_sch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]
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2025-07-13 ubida de simulasiones de diseño de 0-10V, entradas digitales aisladas y salida a relay funcionales
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2025-07-17 Placa inverter al 90%
    [Conector P2.54mm 2P Male.SLDPRT, Conector P2.54mm 2P Male.step, Conector P2.54mm 3P Male.sldprt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]
2025-07-18 Cambios en los periféricos previo al viaje para poder seguir trabajándolo
    [MCU.kicad_sch, Perifericos.kicad_sch]
2025-07-27 Termino de hacer las simulaciones de los periféricos. Completo los valores de componentes en esquemáticos
    [Fuentes.kicad_sch, MCU.kicad_sch, Perifericos.kicad_sch]
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2025-07-28 Esquematico del programador del ESP para no tener que meter la mano sobre la placa para resetear y meter en modo debug. Solo se agrega un header en el PCB del HMI con los pines de comunicación y cont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
    [ESP_Programmer.kicad_pcb, ESP_Programmer.kicad_sch]
2025-07-28 Terminado el esquemático del HMI
    [Fuentes.kicad_sch, HMI_LVDC-Inverter.kicad_sch, MCU.kicad_sch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]
2025-07-28 Avance en placas micro cnv inv e inter
    [3303W-3.step, Conector Banana Socket 1P Negro.sldprt, Conector Banana Socket 1P Negro.step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]
2025-07-29 Terminado el programador de ESp
    [ESP_Programmer.kicad_pcb, ESP_Programmer.kicad_sch]
2025-07-29 Normalizacion placa micros
    [InterfazConexion.kicad_sch, VFD_V1.kicad_pcb, VFD_V1.kicad_sch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]
2025-07-30 Avance con el esquemático, faltan definir algunas etiquetas que no las encontré
    [Fuentes.kicad_sch, HMI_LVDC-Inverter.kicad_sch, MCU.kicad_sch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]
2025-08-05 Terminado todo el conexionado eléctrico esquemático
    [ESP32.kicad_sch, Fuentes.kicad_sch, HMI_LVDC-Inverter.kicad_sch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]
2025-08-06 Avances en PCB conversor y inversor - Simulaciones de modulacion
    [EntradaOptoacopladaNH.kicad_sch, EntradaOptoacopladaNL.kicad_sch, InterfazConexion.kicad_sch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]
2025-08-09 Agregado de los componentes con links de compra en KiCAD a excepción de los conectores
    [ESP32.kicad_sch, Fuentes.kicad_sch, HMI_LVDC-Inverter.kicad_sch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]
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2025-08-13 Avances en el PCB, arreglos en el esquema y agregado de borneras de gabinete
    [ESP32.kicad_sch, Fuente_ISO.kicad_sch, Fuentes.kicad_sch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]
2025-08-13 Avance en el PCB
    [HMI_LVDC-Inverter.kicad_pcb]
2025-08-18 Falta resolver los pulsadores
    [ESP32.kicad_sch, Fuentes.kicad_sch, HMI_LVDC-Inverter.kicad_pcb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]
2025-08-20 Corrección de diseño de control de relay por subdimensión de corriente de colector de optoacoplador
2025-08-20 Agregado y corrección de borneras
    [ESP32.kicad_sch, Fuente_ISO.kicad_sch, Fuentes.kicad_sch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]
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2025-08-21 Eliminacion de placa Cnv-Inv-InterfazPwr
    [3303W-3.step, Conector Banana Socket 1P Negro.sldprt, Conector Banana Socket 1P Negro.step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]
2025-08-21 Actualizacion placa conversor
    [3303W-3.step, Conector P2.54mm 2P Male.step, Conector P2.54mm 5P Male.step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]
2025-08-21 Actualizacion placa inversor
    [Conector P2.54mm 2P Male.step, Conector P2.54mm 4P Male.step, Conector P5.08mm 2P Male.step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]
2025-08-21 Actualizacion placa interfaz
    [Conector Banana Socket 1P Negro.step, Conector Banana Socket 1P Rojo.step, Conector P2.54mm 2P Male.step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]
2025-08-25 Terminada la placa del HMI con revisión de reglas de diseño
    [ESP32.kicad_sch, HMI_LVDC-Inverter.kicad_pcb, HMI_LVDC-Inverter.kicad_sch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]
2025-08-25 Cambio de pin de 0-10V
    [ESP32.kicad_sch, HMI_LVDC-Inverter.kicad_pcb]
2025-08-30 Actualizacion conversor
    [EDT42.step, MedicionCorriente.kicad_sch, MedicionTension.kicad_sch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]
2025-08-30 Actualizacion Inversor
    [PCB_Inversor.kicad_pcb, inversor.kicad_sch]
2025-08-30 Actualizacion PCB MicroHMI
    [DG250-3.5-03P-11-00A&Z(H).stp, DG250-3.5-08P-11-00A&Z(H).stp, ESP32.kicad_sch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]
2025-08-30 Subida PCB integradora
    [Conector Banana Socket 1P Negro.step, Conector Banana Socket 1P Rojo.step, Conector P2.54mm 2P Male.step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]
2025-09-01 Actualizacion convesor
    [PCB_Conversor-B_Cu.gbr, PCB_Conversor-B_Mask.gbr, PCB_Conversor-B_Paste.gbr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]
2025-09-01 Actualizacion MicroHMI
    [HMI_LVDC-Inverter-B_Cu.gbr, HMI_LVDC-Inverter-B_Mask.gbr, HMI_LVDC-Inverter-B_Paste.gbr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]
2025-09-01 Actualizacion placa integradora
    [Conector Banana Socket 1P Negro.step, Conector Banana Socket 1P Rojo.step, Conector P2.54mm 2P Male.step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]
2025-09-01 Modelo 3D - Al 80%
    [Bornera3P.SLDPRT, Bornera8P.SLDPRT, Boton.SLDPRT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]
2025-09-04 Firmware STM32 - Error delay calculo
    [GestorEstados.c, GestorSVM.c, GestorSVM.h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]
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2025-09-18 Avances con el driver del MCP23017 y primera demo de display con edición de variables
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2025-10-28 HMI funcional para primeras pruebas. Resta linealizar bien los ADC más correcciones de pruebas
2025-11-17 Agregado de documentación con Doxygen Agregado de pantalla de emergencia TODO: Documentarla Modularización de todo el software Mejoras en las mediciones del ADC para una menor variabilidad de la medi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
2025-11-17 Corrección en la respuesta al ESP32 para no recibir como respuesta '0'
2025-11-17 Corrección en el gestor de estados para poder cambiar la velocidad en medio de un cambio una aceleración o desaceleración
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2025-11-22 Cambio para no permitir arrancar el motor mientras que no se saque el pulsador de emergencia, se salga de la condición de emergencia por seguridad y el termoswitch se desactive
2025-11-23 - Corrección en la secuencia de inicio del ADC - Cambio en la lectura del estado lógico del pulsador de para de emergencia
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2025-12-06 Correción de bugs en la integración WiFi-Sistema
    [display.c, rtc.c]
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2025-12-16 Descarga de la tesina desde overleaf y arreglos en el *.bib Falta citar en donde corresponda
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

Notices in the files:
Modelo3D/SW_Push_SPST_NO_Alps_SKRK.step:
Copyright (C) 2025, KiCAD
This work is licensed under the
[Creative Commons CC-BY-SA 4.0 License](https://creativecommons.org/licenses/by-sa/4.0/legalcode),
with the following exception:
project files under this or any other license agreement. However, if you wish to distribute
